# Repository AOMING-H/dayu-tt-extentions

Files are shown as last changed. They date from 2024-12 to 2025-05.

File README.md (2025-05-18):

# 大鱼TT 3D打印机拓展
## 切刀拓展
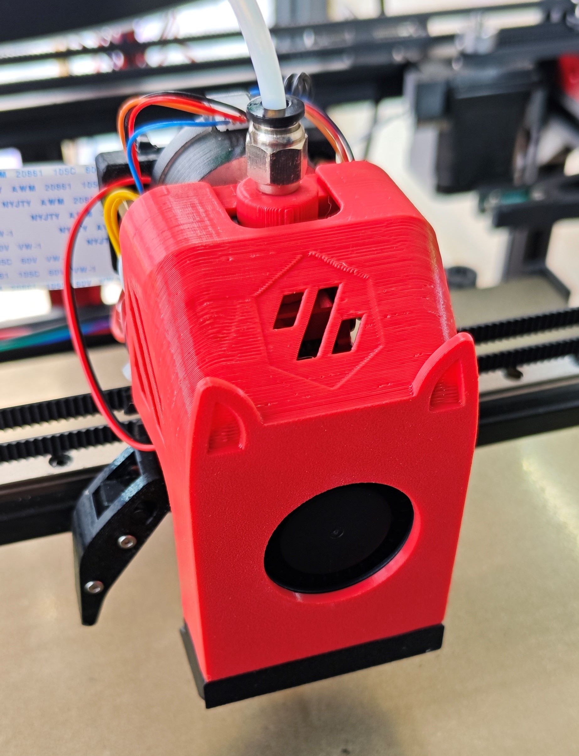
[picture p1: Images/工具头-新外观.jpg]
工具头-正面


参考两位B站UP以及兔子多色切刀工具头的设计

汪汪队射手: https://www.bilibili.com/video/BV19w4m1k7Eu

月下客KS: https://www.bilibili.com/video/BV1WHpde1ECP
### 特性
- 双耗材传感器, 上方传感器可根据实际需求进行添加
- 使用4号刀片, 杠杠切割更省力
- 接近开关替换为Klicky, 没有温漂更稳定
- 兼容TT原风道, 理论无行程损失(有封箱需要进行加高)

### 打印注意事项
- 建议使用ABS进行打印
- 建议使用Voron结构件打印参数进行打印
    - 顶底5层, 壁厚4, 填充40%
- 请自行观察模型, 加上支撑

## 交流QQ群
1027251200

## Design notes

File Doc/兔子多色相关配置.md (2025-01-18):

本文档仅针对大鱼TT310版本以及本工程所分享的挤出头有效, 其它版本请自行进行调整

本文档不详细介绍如何进行多色调试, 仅提供对应配置文件, 详细多色调试请参考胖松鼠分享的文档以及对应视频

https://docs.qq.com/doc/DQndFeFp6RUZ0eHli

## 一些建议
- IO口足够的情况下, 建议使用挤出头双传感器, 并更换 extruder_homing_endstop 为 extruder 归位
    - 这里按双传感器配置进行说明
- 舵机推荐更换, MG90S勉强能用, 更换国华9g舵机下压力大很多, 调试会更顺利
- 同步挤出建议加装, 仅36电机可能拉不动耗材
- 如果在手动上料的时候发需要很大力才拉得动, 请检解决进料顺畅程度
- 兔子多色挤出步进电机推荐把352电机换成42电机, 可以配合1:2的减速比或者直驱MOD加快耗材更换速度
- 编码器的623V轴承由于深度不一样, 在校准编码器的时候如果一直有较大的误差, 可以更换为普通的623轴承以及对应打印件

## printer.cfg文件引用
前两个为兔子多色需要的引用
后两个分别为 klicky和喷嘴清理所需要 的引用
```
[include mmu/base/*.cfg]
[include mmu/optional/client_macros.cfg]
[include euclid.cfg]
[include wipe-nozzle.cfg]
```
保存后重启, 并确认归位操作正常

## mmu/base/mmu.cfg
如果是使用我的开源主板, 可参考以下配置
 - https://oshwhub.com/aoming/ji-yu-stm32c8t6-hu-xin-ban-di-tu-zi-duo-se-zhu-ban
```
[board_pins mmu]
mcu: mmu # Assuming using an external / extra mcu dedicated to MMU
aliases:
    MMU_GEAR_UART=PB10,
    MMU_GEAR_STEP=PB1,
    MMU_GEAR_DIR=PB0,
    MMU_GEAR_ENABLE=PB11,
    MMU_GEAR_DIAG=,
    MMU_SEL_UART=PA0,
    MMU_SEL_STEP=PC15,
    MMU_SEL_DIR=PC14,
    MMU_SEL_ENABLE=PA1,
    MMU_SEL_DIAG=,
    MMU_SEL_ENDSTOP=PB14,
    MMU_SERVO=PA2,
    MMU_ENCODER=PA5,
    MMU_GATE_SENSOR=,
    MMU_NEOPIXEL=PA6,
    MMU_PRE_GATE_0=PB15,
    MMU_PRE_GATE_1=PB5,
    MMU_PRE_GATE_2=PB4,
    MMU_PRE_GATE_3=PB3,
    MMU_PRE_GATE_4=PA15,
    MMU_PRE_GATE_5=PA10,
    MMU_PRE_GATE_6=PA9,
    MMU_PRE_GATE_7=PA8,
    MMU_PRE_GATE_8=,
    MMU_PRE_GATE_9=,
    MMU_PRE_GATE_10=,
    MMU_PRE_GATE_11=,
    MMU_BELAY=PB13,
```

## mmu/base/mmu_macro_vars.cfg
以下为需要修改的配置, 请找到对应位置进行替换
```
variable_cutting_axis		    : "x"		; 切断耗材时, 工具头的运动方向
variable_pin_loc_xy             : 15, 280	; 切刀臂刚接触撞击块的坐标, 请自行调整
variable_pin_park_dist          : 5.0		; 切刀动作前加速的距离
variable_pin_loc_compressed     : 1.0		; 最后压缩状态的X坐标, 这里设置过头会丢步

variable_blade_pos              : 46.5		; 切割刀片刀喷嘴尖端的距离
variable_retract_length         : 30.0		; 切割之前回抽的距离

# 以下为换料过程中停车位置
variable_park_toolchange        : -1, -1, 1, 5, 2	; x,y,z-hop,z_hop_ramp,retract for "toolchange" operations (toolchange,load,unload)
variable_park_runout            : -1, -1, 1, 5, 2	; x,y,z-hop,z_hop_ramp,retract
variable_park_pause             : 50, 310, 5, 0, 2	; x,y,z-hop,z_hop_ramp,retract (park position when mmu error occurs)
variable_park_cancel            : -1, -1, 10, 0, 5	; x,y,z-hop,z_hop_ramp,retract
variable_park_complete          : 50, 310, 10, 0, 5	; x,y,z-hop,z_hop_ramp,retract

variable_pre_unload_position    : -1, -1, 0	; x,y,z-hop position before unloading starts
variable_post_form_tip_position : -1, -1, 0	; x,y,z-hop position after form/cut tip on unload
variable_pre_load_position      : 3, 310, 0	; x,y,z-hop position before loading starts, 
variable_restore_xy_pos         : "next"	; 控制工具头（x,y）在执行停车动作后的返回位置 

variable_user_post_form_tip_extension       : 'MOVE_TO_WIPE_NOZZLE_POS'	; 尖端成型之后执行的宏
variable_user_post_load_extension           : 'WIPE_NOZZLE'	            ; 加载料之后执行的宏
```

## mmu/base/mmu_hardware.cfg
stepper_mmu_gear 和 stepper_mmu_selector 可适当调整挤出机电流和其他参数
以下为需要修改的配置, 请找到对应位置进行替换
```
extruder_switch_pin: PB13                   # 挤出机传感器上, 请自行更换对应引脚
toolhead_switch_pin: PA13                   # 挤出机传感器下, 请自行更换对应引脚
sync_feedback_tension_pin: ^mmu:MMU_BELAY   # 在灯丝张力下触发的开关传感器
sync_feedback_compression_pin:              # 在灯丝压缩下触发的开关传感器

# 以下为LED配置, 请根据实际情况进行调整
[neopixel mmu_leds]
pin: mmu:MMU_NEOPIXEL
chain_count: 16			# 门的数量 x1 or x2 + 1 (如果你有状态LED)
color_order: GRB		# 设置neopixel灯珠的规格顺序

[mmu_leds]
led_strip: neopixel:mmu_leds
exit_range: 8-1
entry_range: 9-16
#status_index: 9
frame_rate: 24

```

## mmu/base/mmu_parameters.cfg
以下为需要修改的配置, 请找到对应位置进行替换
```
gear_max_velocity: 100			# 耗材加载速度上限, 请根据个人情况修改
gear_max_accel: 500			    # 耗材加载加速度上限, 请根据个人情况修改
selector_max_velocity: 200		# 选料电机速度上限, 请根据个人情况修改
selector_max_accel: 1200		# 选料电机加速度上限, 请根据个人情况修改

gear_from_buffer_speed: 80		# 从缓存区加载耗材的速度, 请根据个人情况修改
gear_from_buffer_accel: 100		# 从缓存区加载耗材的加速度, 请根据个人情况修改
gear_from_spool_speed: 80		# 从料盘加载耗材的速度, 请根据个人情况修改
gear_from_spool_accel: 100		# 从料盘加载耗材的加速度, 请根据个人情况修改

toolhead_extruder_to_nozzle: 82.0		# 挤出机齿轮啮合位置到喷嘴尖端的距离
toolhead_sensor_to_nozzle: 53.3		    # 工具头传感器（挤出机下方）到喷嘴尖端的距离
toolhead_entry_to_extruder: 19.4		# 挤出机入口传感器到挤出机啮合位置的距离
toolhead_residual_filament: 23		    # 喷嘴中耗材卸载后残留耗材长度(对于大流量热端，比如TZ2.0，此值比较大，大约23)
toolhead_ooze_reduction: 2		        # 修复最后可能的漏料问题，一般是一个很小的数，大于零表示减少加载量

extruder_homing_max: 120			    # 耗材慢速加载的最大距离
extruder_homing_endstop: extruder	    # 耗材加载到位检测方式, 这里直接指定使用挤出机上方传感器
extruder_homing_buffer: 25			    # 鲍登长度减掉这个距离, 然后慢速靠近微动
extruder_collision_homing_current: 50	# 归位到挤出机时使用的步进电机电流（10%-100%）
extruder_force_homing: 1                # 强制开始挤出机归位, 避免进料时出现剧烈碰撞

force_form_tip_standalone: 1		    # 使用快乐兔全权负责尖端处理
form_tip_macro: _MMU_CUT_TIP            # 调用快乐兔切刀的宏

sync_to_extruder: 1			# 在打印过程中使兔子的齿轮送料电机和挤出机电机同步，设置为1
sync_gear_current: 70		# 百分比% 在同步挤出时，齿轮送料电机的电流为正常状态的百分比(10%-100%)
sync_form_tip: 1			# 尖端处理的时候是否采用同步

sync_feedback_enable: 1			# 0 = 关闭 (即使安装了传感器), 1 = 开启(仅在打印过程中)
sync_multiplier_high: 1.15		# 应用于齿轮步进器“旋转_距离”的最大系数, 请根据个人情况修改
sync_multiplier_low: 0.95		# 应用于齿轮步进器“旋转_距离”的最小系数, 请根据个人情况修改

retry_tool_change_on_error: 1	# 开启错误自动恢复

gate_preload_homing_max: 200		# 耗材就位的拉取距离
```

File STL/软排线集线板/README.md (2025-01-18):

软排线集线板地址以及对应BOM请见

https://oshwhub.com/zyuel/ji-xian-ban

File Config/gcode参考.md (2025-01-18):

以下为TT310参考gcode, 其它尺寸请自行调整

打印起始:
```
M190 S[first_layer_bed_temperature] ; 等待热床升温
M109 S150 ; 先升温到150

; 初始化MMU相关的宏
MMU_START_SETUP INITIAL_TOOL={initial_tool} REFERENCED_TOOLS=!referenced_tools! TOOL_COLORS=!colors! TOOL_TEMPS=!temperatures! TOOL_MATERIALS=!materials! PURGE_VOLUMES=!purge_volumes!

; 调用MMU开始检查
MMU_START_CHECK

EUCLID_PROBE_BEGIN_BATCH  ; klicky 批量模式开启
BED_MESH_CLEAR ; 卸载网床
G28 ; 各轴归位
G90 ; 启用绝对坐标
Z_TILT_ADJUST ; 三点调平
BED_MESH_PROFILE LOAD='default' ; 加载网床
G28 ; 各轴归位
EUCLID_PROBE_END_BATCH  ; klicky 批量模式结束

G1 X5 Y310 F5000.0  ; 移动到擦嘴位置

M109 S[first_layer_temperature] ; 等待挤出机升温
#加载第一个耗材
MMU_START_LOAD_INITIAL_TOOL

G92 E0 ; 重置挤出机
G1 X20 Y270 Z0.3 F5000 ; 移动到第一条线开始
G1 X20 Y200 Z0.2 F1500 E15 ; 画第一条线
G1 X20 Y200 Z0.3 F5000 ; 往上面移动一点准备画第二条线
G1 X20 Y270 Z0.2 F1500 E15 ; 画第二条线
G92 E0 ; 重置挤出机
G1 Z1.0 F500 ; 抬升Z轴，准备移动到模型打印区域
```

打印结束:
```
G91 ; 启用相对位置
G0 Z1.00 X20.0 Y20.0 F5000    ; 移动喷嘴以拆除架线
M107  ; 关闭模型风扇
G1 Z2 F500    ; 抬高Z轴

MMU_END ; 关闭mmu
TURN_OFF_HEATERS ; 关闭加热

G90   ; 启用绝对位置
G1 X20 F5000
G1 Y250 F5000 ; 停靠打印头

BED_MESH_CLEAR  ; 卸载床网
;M84 ; 关闭电机
PRINT_END ; 打印结束
```

取消打印:
```
BED_MESH_CLEAR  ; 卸载床网
MMU_END ; 结束换色
TURN_OFF_HEATERS
CANCEL_PRINT_BASE
G1 X20 F5000
G1 Y250 F5000 ; 移动到停泊位置
M106 S0 ; 关闭模型风扇
#M84 ; 关闭电机
```

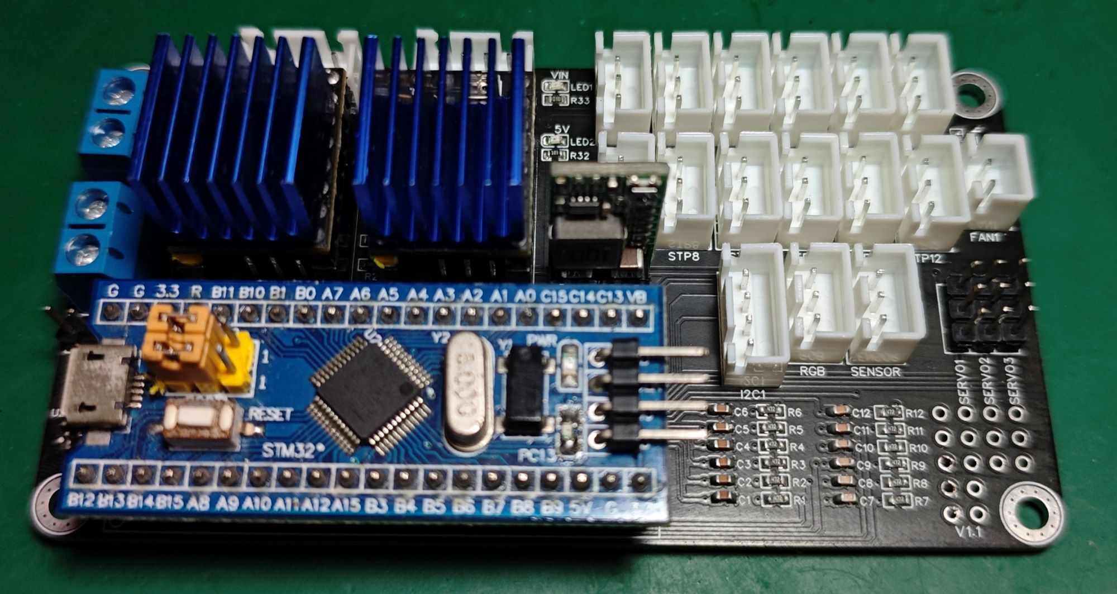
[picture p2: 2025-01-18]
Images/使用的兔子多色主板.jpg

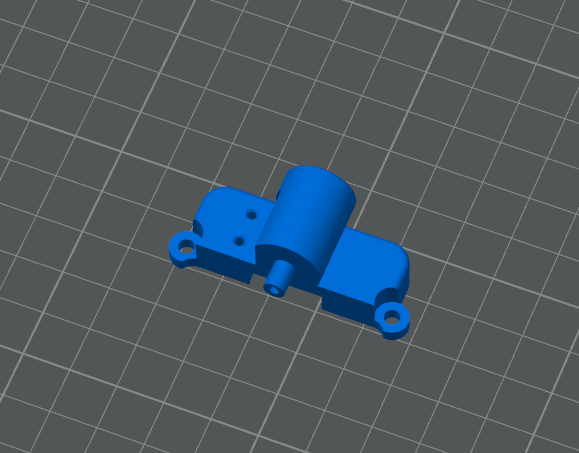
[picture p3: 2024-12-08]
Images/上置传感器摆放方向.jpg

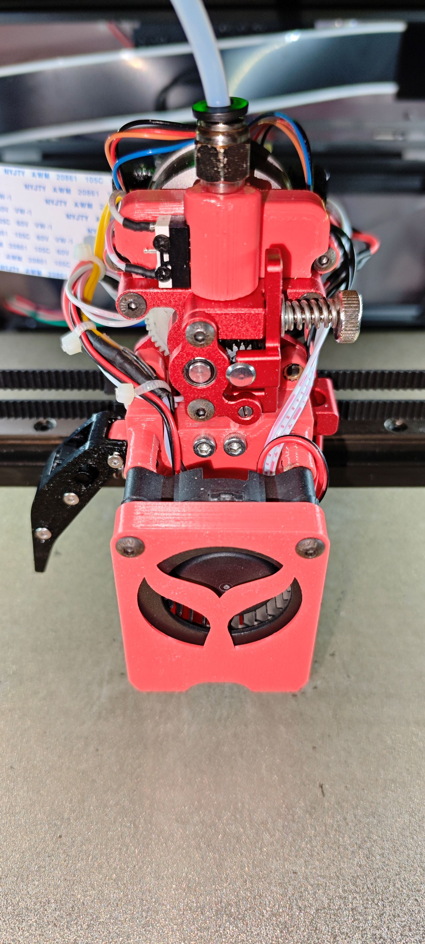
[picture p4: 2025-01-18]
Images/工具头-正面.jpg

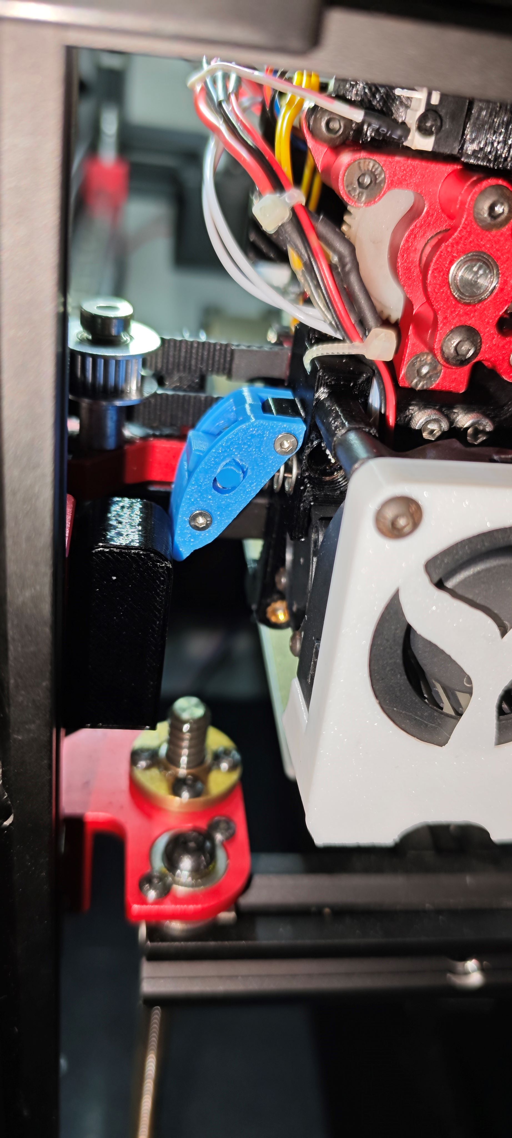
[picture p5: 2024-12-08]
Images/切刀测试-释放.jpg

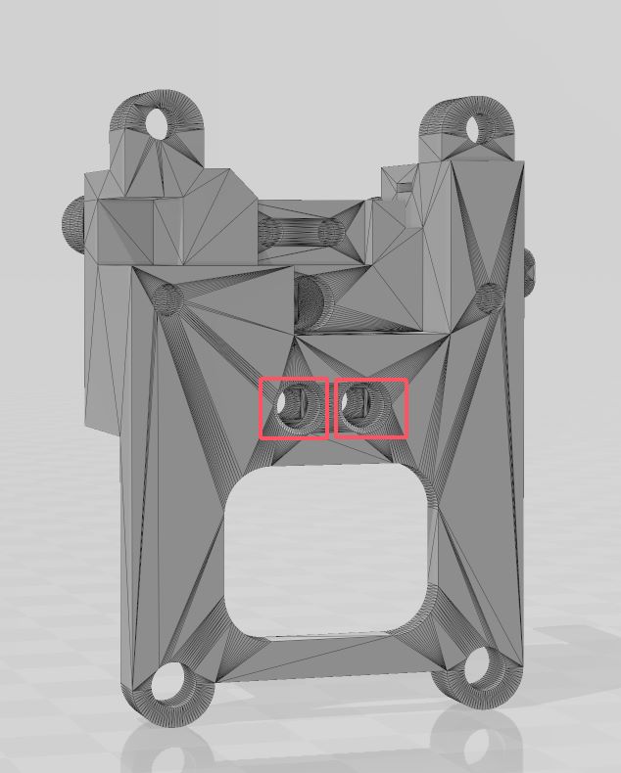
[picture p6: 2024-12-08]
Images/切刀改装-主体-热熔螺母说明2.jpg

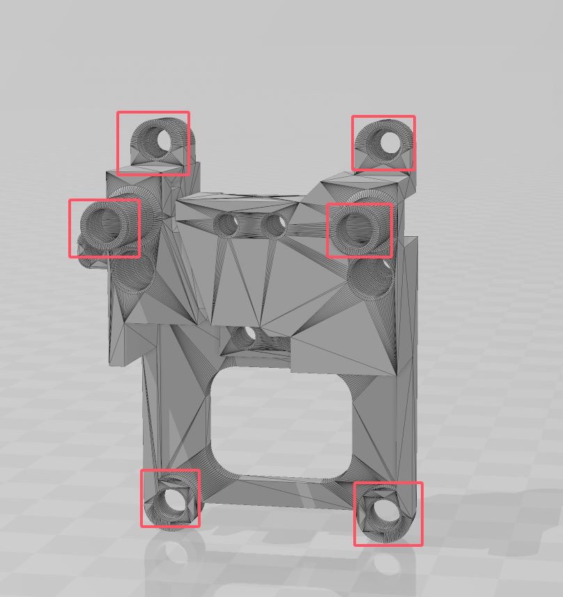
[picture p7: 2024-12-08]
Images/切刀改装-主体-热熔螺母说明1.jpg

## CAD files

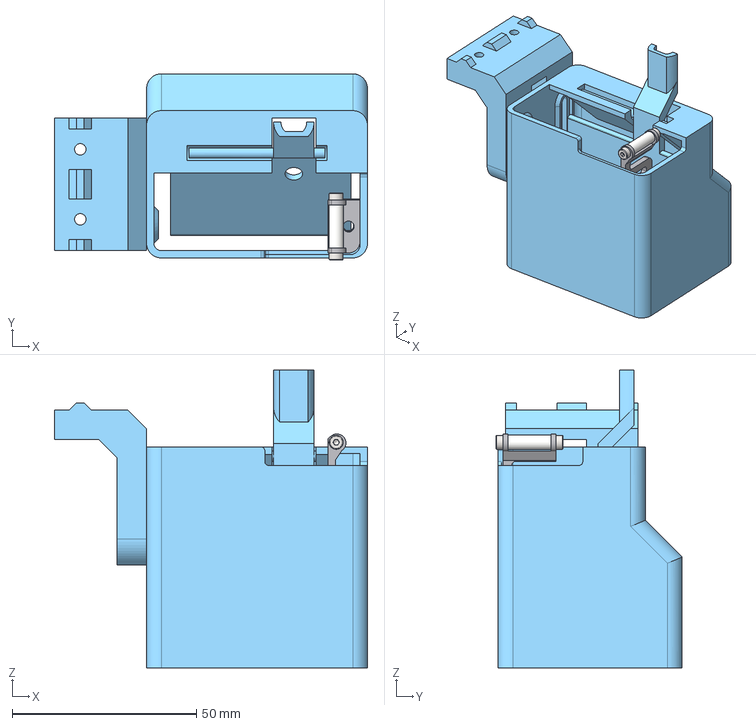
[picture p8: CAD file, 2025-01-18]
CAD/喷嘴清理.stp
85.0 x 50.6 x 80.9 mm

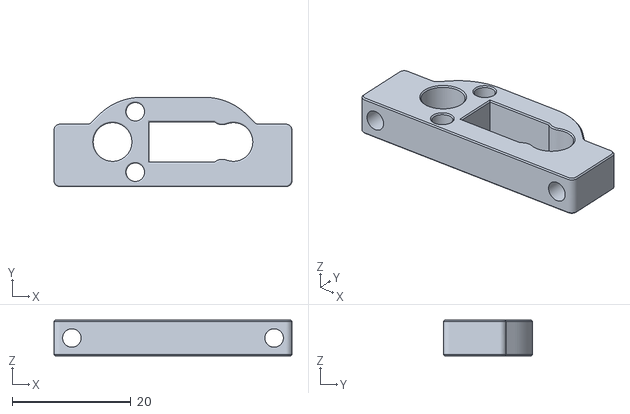
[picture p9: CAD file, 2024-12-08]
STL/Klicky/Klicky-支架.stl
40.0 x 15.0 x 6.00

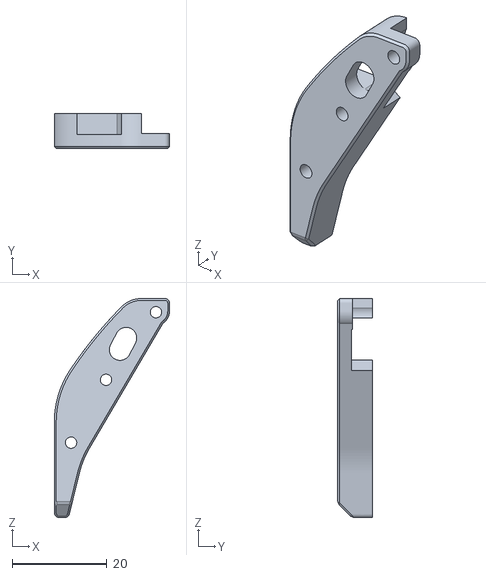
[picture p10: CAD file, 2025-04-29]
STL/切刀臂-加长版/切刀改装-切刀臂V2-2.stl
24.4 x 7.35 x 46.3

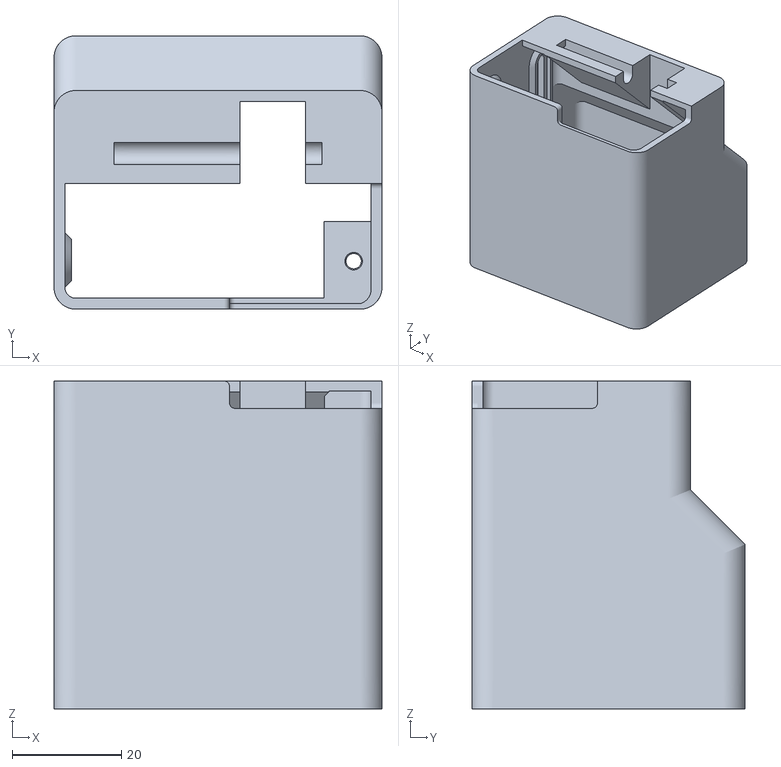
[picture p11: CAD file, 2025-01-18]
STL/喷嘴清理-加盖版/喷嘴清理-排料通道.stl
60.0 x 50.0 x 60.0

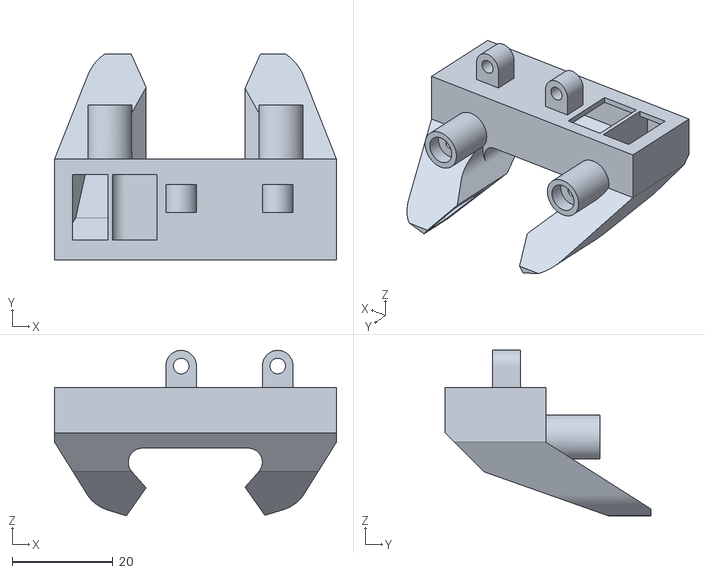
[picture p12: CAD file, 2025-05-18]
STL/挤出头/[5015风道外观优化]-模型散热-风道2.stl
56.0 x 40.9 x 32.9

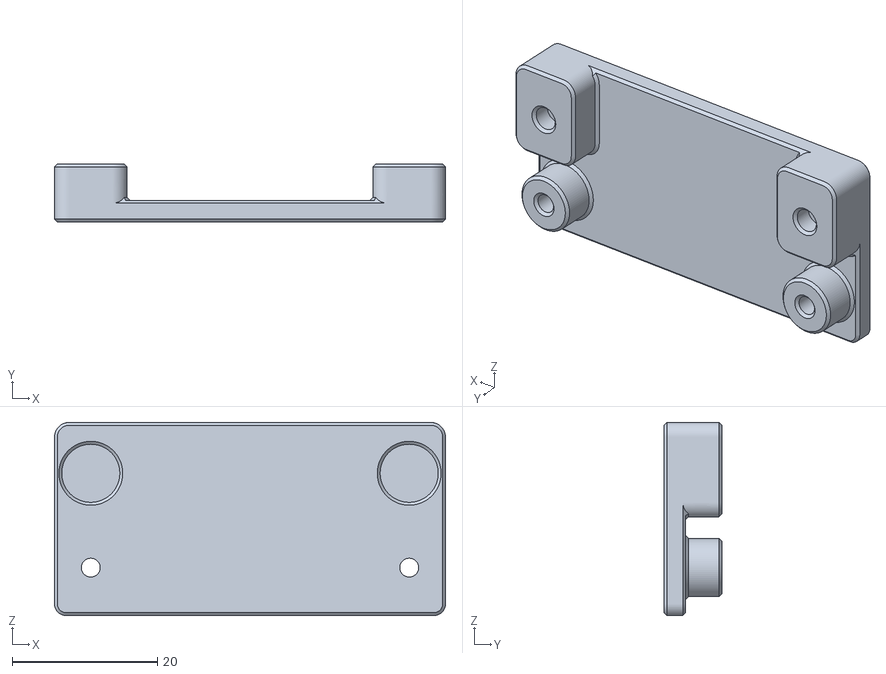
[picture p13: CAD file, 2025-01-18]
STL/软排线集线板/集线板支架.stl
53.9 x 8.00 x 26.6

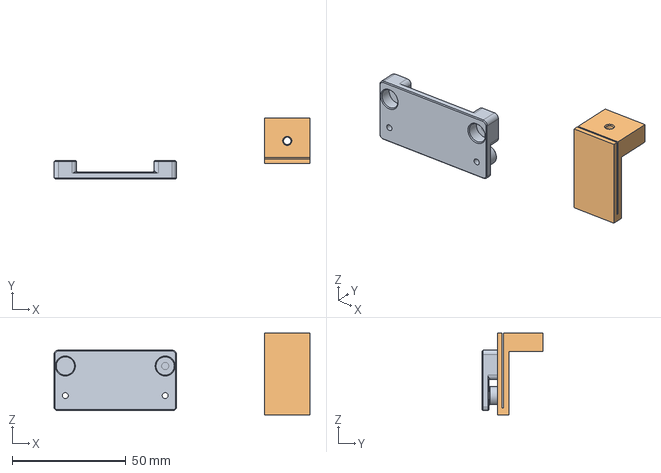
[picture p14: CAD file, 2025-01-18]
CAD/软排线集线板.stp
112.5 x 26.7 x 36.0 mm

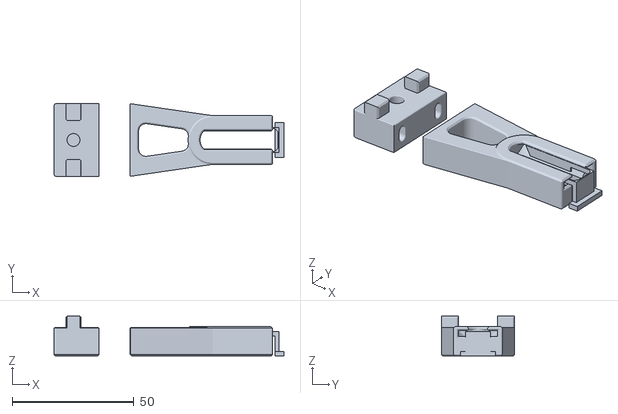
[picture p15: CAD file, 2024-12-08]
STL/Klicky/Klicky-停靠坞.stl
94.4 x 30.0 x 16.4

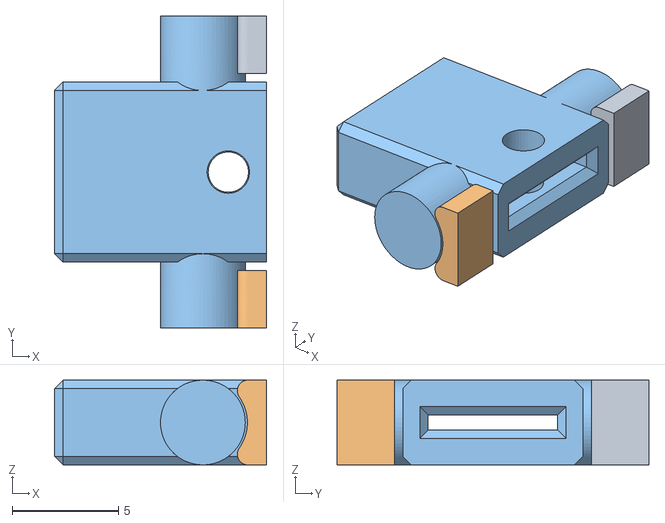
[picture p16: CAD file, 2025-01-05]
STL/切刀臂-加长版/切刀改装-切刀臂V2-3(刀片直通).stl
10.0 x 14.7 x 4.00

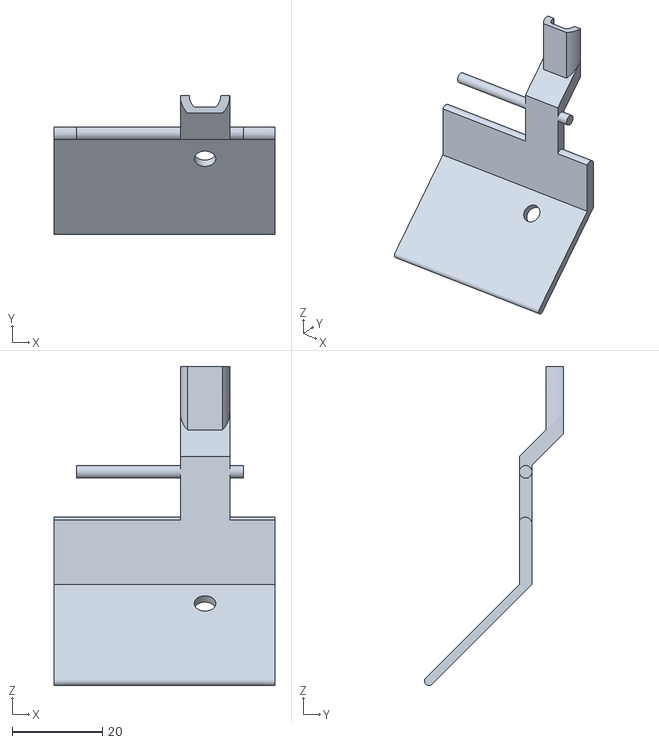
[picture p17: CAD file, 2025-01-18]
STL/喷嘴清理-加盖版/喷嘴清理-接料盖.stl
49.0 x 30.9 x 70.9

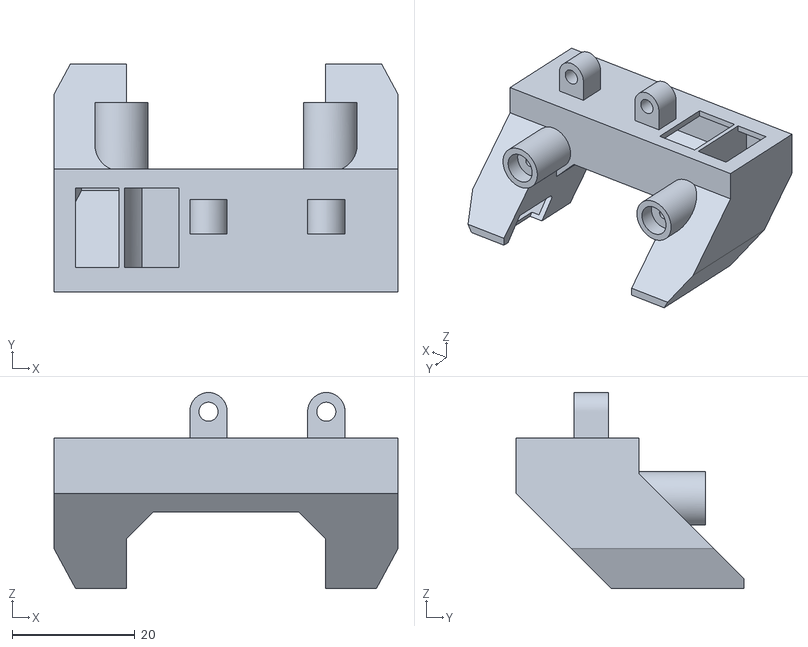
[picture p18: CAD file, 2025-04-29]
STL/挤出头/[5015风道外观优化]-模型散热-风道1.stl
56.0 x 37.1 x 31.9

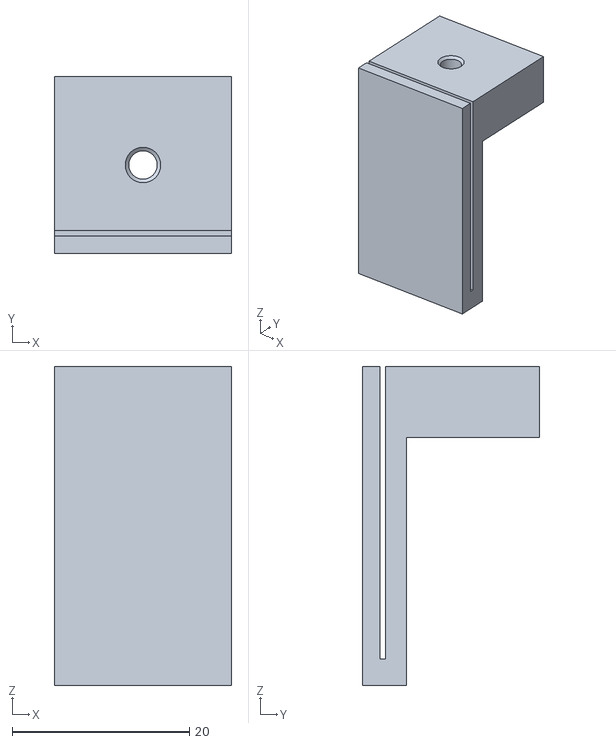
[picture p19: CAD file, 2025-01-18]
STL/软排线集线板/软排线支架.stl
20.0 x 20.0 x 36.0

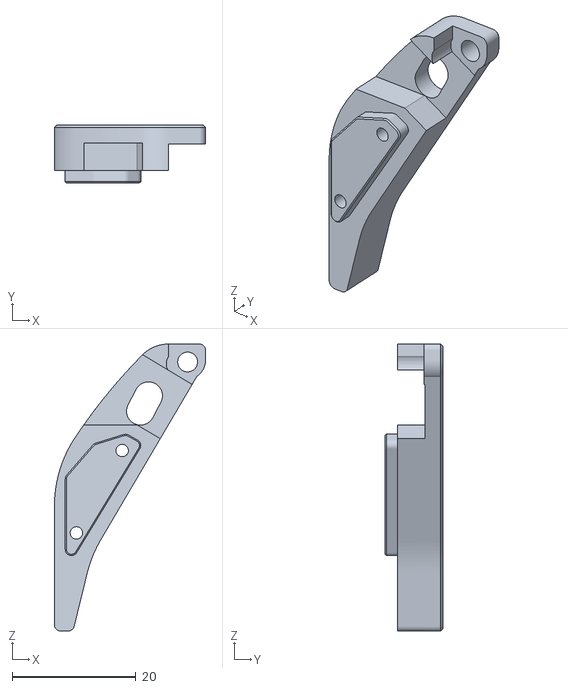
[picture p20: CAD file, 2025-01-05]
STL/切刀臂-加长版/切刀改装-切刀臂V2-1.stl
24.4 x 9.35 x 46.3

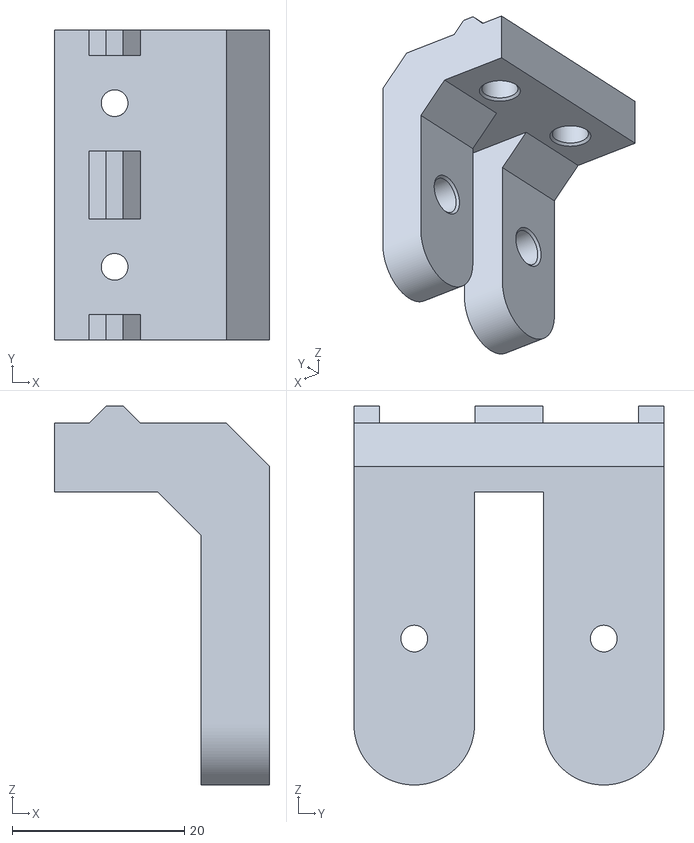
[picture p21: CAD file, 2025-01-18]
STL/喷嘴清理-加盖版/喷嘴清理-安装支架.stl
25.0 x 36.0 x 44.0

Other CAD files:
STL/挤出头/[5015风道外观优化]-耗材传感器上-PC4M6.stl
STL/切刀臂-加长版/切刀改装-撞击座V2-前装版.stl
STL/喷嘴清理-加盖版/喷嘴清理-擦嘴支架.stl
STL/挤出头/[4020~5015风道通用二选一]-耗材传感器上-鲍登头.stl
STL/切刀臂-加长版/切刀改装-切刀臂V2-3.stl
STL/切刀臂-加长版/切刀改装-撞击座V2-下装版.stl
STL/挤出头/[4020~5015风道通用二选一]-耗材传感器上-PC4M6.stl
STL/旧版本/切刀臂-原版(弃用)/切刀改装-切刀臂1.stl
STL/旧版本/切刀臂-原版(弃用)/切刀改装-切刀臂2.stl
STL/旧版本/切刀臂-原版(弃用)/切刀改装-切刀臂3.stl
STL/旧版本/切刀臂-原版(弃用)/切刀改装-撞击座.stl
STL/旧版本/喷嘴清理/喷嘴清理-安装支架.stl
STL/旧版本/喷嘴清理/喷嘴清理-排料通道.stl
STL/旧版本/喷嘴清理/喷嘴清理-擦嘴支架.stl

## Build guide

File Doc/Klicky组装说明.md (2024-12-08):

Klicky停靠坞暂未修改直接使用汪汪队射手原始版本

停靠坞为分体, 需要两个热熔螺母
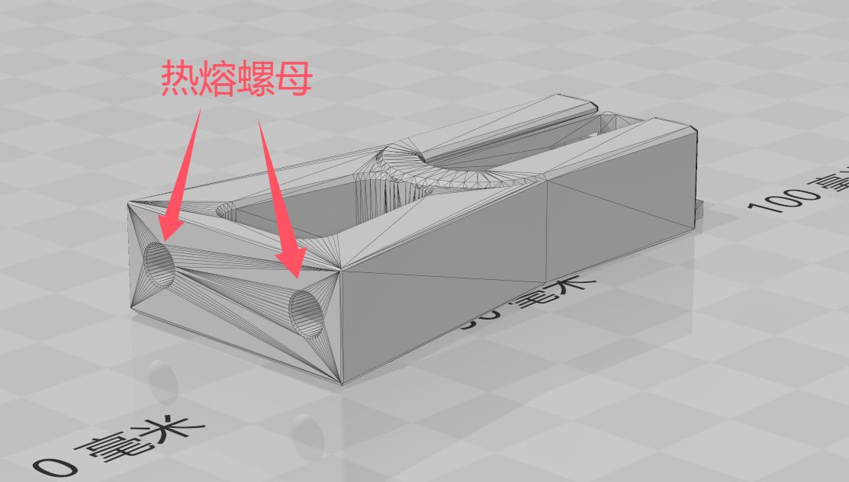
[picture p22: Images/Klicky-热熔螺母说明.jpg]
Klicky-热熔螺母说明


停靠坞安装时可上下调节一段距离, 适配不同高度

测量喷头到微动为2.52mm, 计算得出z_offset约为2.72mm, 根据不同的装配情况可能会有出入

310尺寸机器坐标参数大致如下, 请根据实际情况进行调整
```
variable_position_preflight: [ 270, 270 ] # 【准备部署】 准备取探针的坐标点
variable_position_side:      [ 307, 270 ] # 【停靠坞边缘】 开始取探针的坐标点，速度会变慢
variable_position_dock:      [ 307, 310 ] # 【停靠坞】 取到探针的坐标点，会经行部署断言
variable_position_zstop:     [ 155, 155 ] # z限位坐标，如何使用请设置
variable_position_exit:      [ 270, 310 ] # 【停靠坞出口】 取完探针的坐标点
```

Probe offset参考
```
x_offset: -1.95
y_offset: 22.00
```

310尺寸机器三点调平坐标参考
```
points:
  20,20
  155,270
  290,20
```

310尺寸机器床网坐标参考
```
mesh_min: 10,25
mesh_max: 290,300
```

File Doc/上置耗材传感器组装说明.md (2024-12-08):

使用上置耗材传感器会增加挤出机高度, 有封箱需要考虑再额外加高

PC4-M6接头款: 19.87mm

鲍登头款: 22.87mm

打印时请放平打印, 耗材进入会较为顺畅, 并自行加上支撑

若微动开关锁上后一直为触发状态, 可以考虑用力按压一下钢珠, 或清理一下钢珠孔, 以留出触发间隙

进料铁氟龙管一定要插到底, 否则进料可能会卡顿

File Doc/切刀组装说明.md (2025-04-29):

# 概要说明

使用本切刀模块增加挤出机高度(约18mm), Z行程不变, 有封箱需要考虑再额外加高

打印时请放平打印, 耗材进入会较为顺畅, 并自行加上支撑

# 特别注意

如果使用新外观面罩,需要注意是否会与前面两个丝杆以及最前面的铝型材干涉, 可能会造成10mm-20mm行程损失(具体看使用的联轴器)

切刀臂请重新打, 不想重打可以用尖嘴钳剪掉一小块

调试的时候请小心一点, 避免将风道干坏

# 安装顺序
1. 安装下置传感器, 安装完成后验证是否正常触发
   
    可以考虑将微动开关引脚折弯后再焊接, 减少干涉情况(焊接难度增加, 且热缩管不好套)

    若微动开关锁上后一直为触发状态, 可以用力按压一下钢珠, 或清理一下钢珠孔, 以留出触发间隙

2. 安装切刀, 安装完成后验证是否能正常切断耗材

3. 使用两个M3*16将拓竹热端和喉管散热固定到切刀模块上
   
   这里需要注意耗材进料的顺畅度, 若出现卡涩, 可以考虑垫纸或打磨打印件调整

4. 切刀模块直接嵌入原挤出机, 再通过四个螺丝(M3*8和M3*14)与原挤出机进行锁定

5. 安装Klicky, 通过两个M3*14螺丝将支架固定到切刀模块上

6. 使用两个M3*12螺丝将挤出机固定到原有X轴CNC件上

7. 使用两个M3*25螺丝将模型散热固定到切刀模块上

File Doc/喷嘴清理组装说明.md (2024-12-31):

# 概要说明

思路来自FZ和胖松鼠的擦嘴模块

需要将热床向前移动5-10mm, 会有行程损失, 具体移动多少, 请根据实际情况调整

安装位置大致如下图所示, 注意不要与热床产生干涉
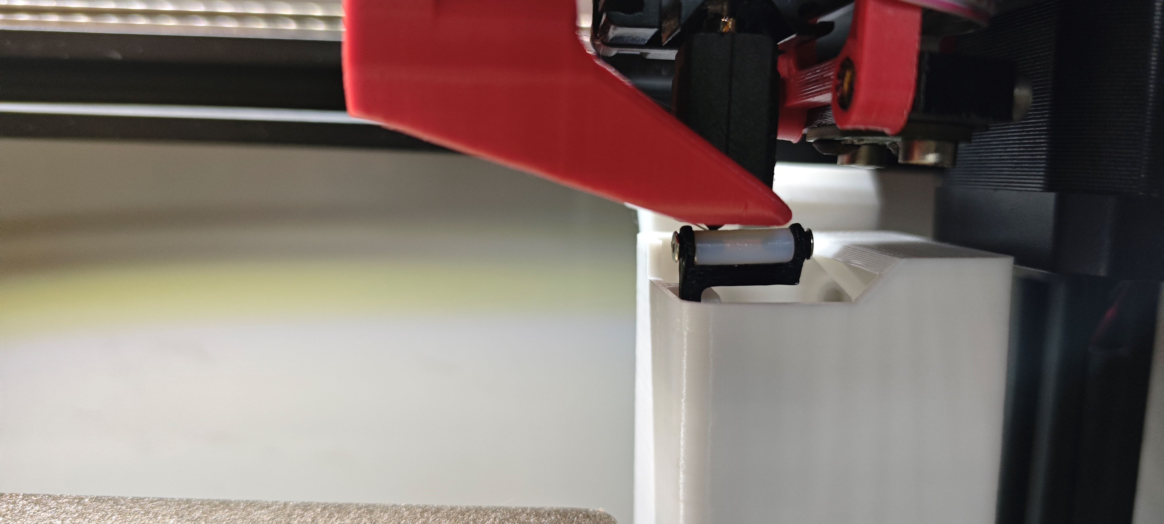
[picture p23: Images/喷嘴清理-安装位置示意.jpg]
喷嘴清理-安装位置示意


# 安装顺序
1. 先将三个打印件组装起来
    - 铁氟龙管按需进行切割
    - 不是很好安装, 需要细心
2. 松开热床, 将喷嘴移动到右上角

3. 安装喷嘴清理模块, 调节前后位置和高度
    - 注意喷嘴刚好能碰到铁氟龙管最佳, 打印件有弹性, 可以碰到没事

4. 重新固定热床
    - 需要注意热床归位的时候不与喷嘴清理模块产生干涉
    - 需要重新做床网补偿

5. 引入配置文件, 加热喷嘴, 调试清理效果
    - 注意原有配置是否延迟执行SET_KINEMATIC_POSITION, 若有请注释, 要不然在未归位情况下会撞机
    - 具体清理效果需要按各自情况进行调试, 调试请调用TEST_WIPE_NOZZLE宏, 
    - 调试完成后 WIPE_NOZZLE 宏也请同步修改, 该宏可读取切片参数传递的冲刷量

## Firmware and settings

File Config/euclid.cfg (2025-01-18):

## The following is EXAMPLE configuration; it is intended to guide you in the
## configuration of the Euclid probe for YOUR printer.
##
## When incorporating this config into your own, make sure you address all
## comment markers starting with "@TODO".  Failure to do so could result in
## damage to your probe, your printer, or your pride.
##
##
## This example is for a fixed dock, fixed gantry/carriage and moving bed motion
## system like RailCore, Ender5, V-Core3, etc. Delta printes will be similar.
##
## Moving gantry printers like Voron need a few tweaks to ensure proper
## clearances and leveling procedures; some hints are provided inline below.
##
## Array variables implementation and macro setups credited to Brian Lalor,
## yolo-dubstep#8033 on Discord. See https://github.com/blalor/vcore3-ratos-config
## for updates and details.
##

## @TODO the following is a hardware probe config for the hardware configuration.
## it can appear in either the printer.cfg OR in the euclid.cfg, not both.
## see https://euclidprobe.github.io/05_klipper.html for more details.
##
##
# [probe]
# ## Euclid probe is on pin ?? on Huvud
# pin: ^PG15
# x_offset: 0
# y_offset: 25
# z_offset: 8.514
# speed: 5
# samples: 2
# samples_result: median
# sample_retract_dist: 5.0
# samples_tolerance: 0.05
# samples_tolerance_retries: 3
# lift_speed: 30

# Below is an example bed diagram to correlate with macros and movements below.
#  __________________________________________________________________________
#  |                                                  X270,Y310   X307,Y310 |
#  |                                                  * 停靠坞出口  * 停靠坞 |
#  |                                                                        |
#  |                                                             X307,Y270  |
#  |                                                             * 停靠坞边缘|
#  |                                                                        |
#  |                                                  X270,Y270             |
#  |                                                  * 准备部署             |
#  |                                                                        |
#  |                                                                        |
#  |                                                                        |
#  |                                                                        |
#  |                                                                        |
#  |                                                                        |
#  |                                                                        |
#  |                                                                        |
#  |                                                                        |
#  |                                                                        |
#  |                                                                        |
#  |                                                                        |
#  |                                                                        |
#  |                                                                        |
#  |                                                                        |
#  |                                                                        |
#  |                                                                        |
#  |                                                                        |
#  |                                                                        |
#  |________________________________________________________________________|
#



[gcode_macro EuclidProbe]
description: config vars for Euclid probe deploy/stow

## @TODO 替换坐标以适合您的打印机
variable_position_preflight: [ 270, 270 ] # 【准备部署】 准备取探针的坐标点
variable_position_side:      [ 307, 270 ] # 【停靠坞边缘】 开始取探针的坐标点，速度会变慢
variable_position_dock:      [ 307, 310 ] # 【停靠坞】 取到探针的坐标点，会经行部署断言
## @TODO 如果使用Z限位就定义它
## @TODO 例如 Voron Trident
variable_position_zstop:     [ 155, 155 ] # z限位坐标，如何使用请设置

## exit/re-entry staging
variable_position_exit:      [ 270, 310 ] # 【停靠坞出口】 取完探针的坐标点
# 存放探针是完全相反的顺序

## 进行拾取探头时工具头和床身之间的间隙
variable_bed_clearance: 15

## probe dock height
## @TODO If the toolhead can move vertically in relation to the probe dock
## @TODO height(such as attached to the be on a moving-gantry printer like a
## @TODO Voron 2.4), set this to the Z position of the probe dock.
# variable_dock_height: 15

## 移动速度
variable_move_speeds: 7000

## internal state variables; not for configuration!
variable_batch_mode_enabled: False
variable_probe_state: None

gcode:
    RESPOND TYPE=command MSG="{ printer['gcode_macro EuclidProbe'] }"


# @TODO 归位覆盖是特定于机器的。 这个例子是针对一个固定龙门/移动床打印机，例如 Rat Rig V-Core 3. 确保您仅在 Klipper 配置中的一处定义了 [homing_override]
# @TODO （通常在这里或在 Printer.cfg 中）。 尤为重要的是要做好确保在尝试将 Z 轴归位之前拾取探头。
[homing_override]
axes: xyz
gcode:
    {% set euclid_probe = printer["gcode_macro EuclidProbe"] %}

    # @TODO 一旦您验证了该评论，请删除此评论和以下内容
    # @TODO 可以在不与床、底座或工具头碰撞的情况下部署探头
    # M112

    G90

    # 强制将床身和工具头分开
    SET_KINEMATIC_POSITION Z=0
    G0 Z{ euclid_probe.bed_clearance } F500

    # 先归位X和Y
    # 这里加判断可以不用重复归位X和Y
    {% if "x" not in (printer.toolhead.homed_axes | lower) %}
        G28 X
        # 将X移动到中间, 避免与擦嘴和切刀产生干涉
        G0 X{ printer.toolhead.axis_maximum.x/2 } F{ euclid_probe.move_speeds }
    {% endif %}


    {% if "y" not in (printer.toolhead.homed_axes | lower) %}
        G28 Y
    {% endif %}



    ## @TODO 如果您使用 Euclid 充当 Z-Endstop，则需要部署它。
    ## @TODO 如果您使用固定 Z 轴，则注释掉下一行
    DEPLOY_PROBE

    # @ TODO  Home Z 位于床中心，配有 Euclid Probe
    G0 X{ printer.toolhead.axis_maximum.x/2 } Y{ printer.toolhead.axis_maximum.y/2 } F{ euclid_probe.move_speeds }
    G28 Z



    # after 'G28 Z' the probe stays in contact with the bed; move it away bed_clearance height.
    # 在“G28 Z”之后，探头与床保持接触； 将其移离 bed_clearance 高度。
    G0 Z{euclid_probe.bed_clearance} F500

    ## @TODO 如果您使用 Euclid 充当 Z-Endstop，则需要部署它。
    ## @TODO 如果您使用固定 Z 轴，则注释掉下一行
    STOW_PROBE


[gcode_macro _ASSERT_PROBE_STATE]
description: ensures probe is in a known state; QUERY_PROBE must have been called before this macro!
gcode:
    ## QUERY_PROBE manually-verified results, when microswitch not depressed
    ## "TRIGGERED" -> 1 :: probe stowed
    ## "open"      -> 0 :: probe deployed
    {% set last_query_state = "stowed" if printer.probe.last_query == 1 else "deployed" %}

    {% if params.MUST_BE != last_query_state %}
        { action_raise_error("expected probe state to be {} but is {} ({})".format(params.MUST_BE, last_query_state, printer.probe.last_query)) }
    {% else %}
        ## all good; update state
        SET_GCODE_VARIABLE MACRO=EuclidProbe VARIABLE=probe_state VALUE="'{ last_query_state }'"
    {% endif %}

# 部署断言
[gcode_macro ASSERT_PROBE_DEPLOYED]
description: error if probe not deployed
gcode:
    # wait for moves to finish, then pause 0.25s for detection
    M400
    G4 P250

    QUERY_PROBE
    _ASSERT_PROBE_STATE MUST_BE=deployed

# 回收断言
[gcode_macro ASSERT_PROBE_STOWED]
description: error if probe not stowed
gcode:
    # wait for moves to finish, then pause 0.25s for detection
    M400
    G4 P250

    QUERY_PROBE
    _ASSERT_PROBE_STATE MUST_BE=stowed


# 开始 euclid 探测批处理模式
[gcode_macro EUCLID_PROBE_BEGIN_BATCH]
description: begin euclid probe batch mode
gcode:
    SET_GCODE_VARIABLE MACRO=EuclidProbe VARIABLE=batch_mode_enabled VALUE=True
    RESPOND TYPE=command MSG="Probe batch mode enabled"

# 结束 euclid 探针批处理模式和回收探针
[gcode_macro EUCLID_PROBE_END_BATCH]
description: end euclid probe batch mode and stow probe
gcode:
    SET_GCODE_VARIABLE MACRO=EuclidProbe VARIABLE=batch_mode_enabled VALUE=False
    RESPOND TYPE=command MSG="Probe batch mode disabled"
    STOW_PROBE
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

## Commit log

2024-12-08 初始化项目
    [BOM.xlsx, Klicky-停靠坞.STL, Klicky-支架.stl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]
2024-12-31 更新喷嘴清理模块
    [BOM.xlsx, wipe-nozzle.cfg, 喷嘴清理-安装支架.stl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]
2025-01-02 更新切刀臂3(加深1mm版)
    [切刀改装-切刀臂3(加深1mm版)3.stl]
2025-01-03 更新klicky配置文件
    [euclid.cfg]
2025-01-05 新增加长切刀臂/新增5015风扇适配/优化4020版本可能出现干涉的情况/整理文件
    [Klicky-停靠坞.STL, Klicky-停靠坞.stl, Klicky-支架.stl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]
2025-01-05 新增刀片直通版刀片固定
    [切刀改装-切刀臂V2-3(刀片直通).stl]
2025-01-07 更新文档
    [BOM.xlsx, euclid.cfg, wipe-nozzle.cfg]
2025-01-08 4010风道上移0.5mm/5015风道上移1.0mm
2025-01-18 新喷嘴清理
    [喷嘴清理-安装支架.stl, 喷嘴清理-排料通道.stl, 喷嘴清理-接料盖.stl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]
2025-01-18 整理文件
    [喷嘴清理-安装支架.stl, 喷嘴清理-排料通道.stl, 喷嘴清理-擦嘴支架.stl]
2025-01-18 软排线集线板
    [软排线支架.stl, 软排线集线板.stp, 集线板支架.stl]
2025-01-18 STP文件更新
    [喷嘴清理.stp]
2025-04-29 更新新外观
    [BOM.xlsx, 切刀改装-切刀臂V2-2.stl, 模型散热-新外观-风道.stl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]
2026-02-10 整理文件命名
    [[4020~5015风道通用二选一]-耗材传感器上-PC4M6.stl, [4020~5015风道通用二选一]-耗材传感器上-鲍登头.stl, [5015风道外观优化]-模型散热-风道1.stl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]
